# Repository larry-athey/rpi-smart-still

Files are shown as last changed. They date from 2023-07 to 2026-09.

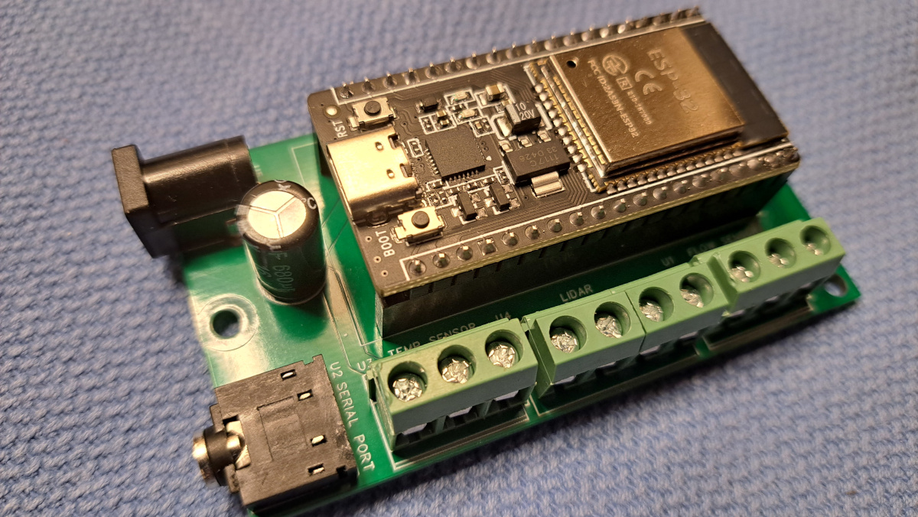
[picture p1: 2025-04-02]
Diagrams/LIDAR Hydrometer Reader/Bird-Brain-PCB-Assembled.jpg

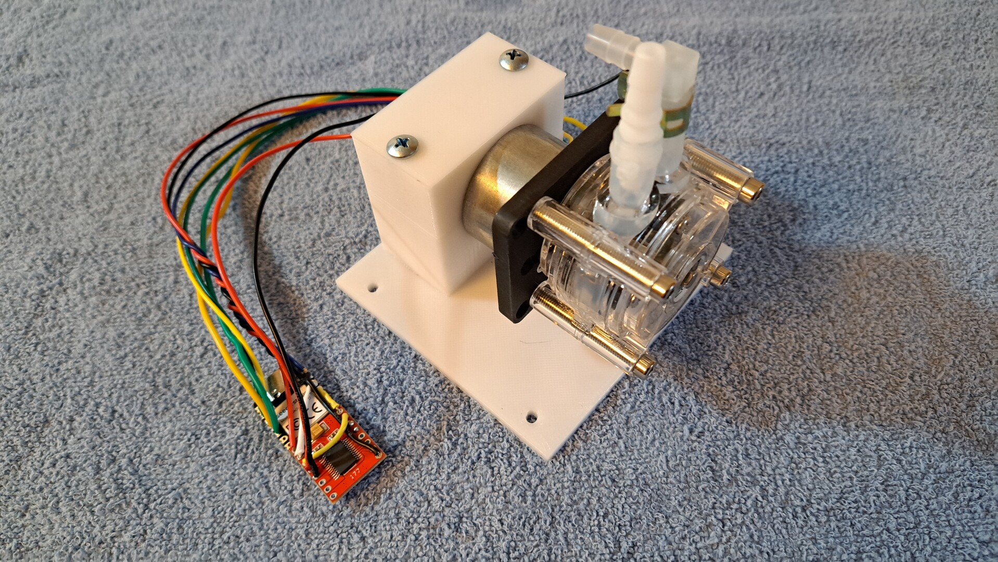
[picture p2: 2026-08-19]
Diagrams/Dephleg Driver/Dephleg Driver 1.jpg

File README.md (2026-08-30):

# RPi Smart Still
Raspberry Pi (or clone) and Arduino/ESP32 powered smart still controller system. Originally designed around the Still Spirits T500 column and boiler, but can be easily added to any other gas or electric still with a dephlegmator. Safe to say that this is the world's first add-on smart still controller because I looked for one before I was forced to build my own. My only other option was to spend $15K on a Genio or iStill...Uh, pass - I'll build one from scratch.

**Please refer to the [Wiki](https://github.com/larry-athey/rpi-smart-still/wiki) for more information and setup/usage instructions.**

**NEWSFLASH:** _Complete [turn-key systems](https://panhandleponics.com/rpi-smart-still-turn-key-systems/) are now available by special order. These systems can vary from the controller-only, all the way up to the controller + LIDAR Hydrometer Reader + Boilermaker + 10" Android tablet + dedicated WiFi router, all pre-configured and ready to plug in._

You may contact me directly at https://panhandleponics.com/contact<br>
Subscribe to the official YouTube channel at https://www.youtube.com/@PanhandlePonics

**Facebook Idiot:** _Why would you bother?_<br>
**Me:** It's only a "bother" for somebody who couldn't do it on their best day. I'd rather have nicer things.

_...No, I don't use AI to design and build my projects, I actually still know how to use my brain..._

---

_**NOTE:** Contrary to a popular misconception, this system does not take away your ability to manually run your still. This system is actually completely stupid until you manually run your still with it and make notes that you would then use to create programs. There is no AI in use here! Every still is different and requires a training period before this system can begin replaying distillation runs. Again, please refer to the [Wiki](https://github.com/larry-athey/rpi-smart-still/wiki), reading is fundamental!_

<br>

Let me start off by saying that I'm no master distiller and I don't pretend to be one. YouTube and other social media sites already have more than enough self-idolizing hacks and frauds _(usually sporting a Popcorn Sutton photo as their profile picture)_ who think that they're legends in the distilling world and should be on the cast of Moonshiners _(a'la, "Cyrus Mason" and "Windsong", the Still'n The Clear charlatans)_. **I'm just a nobody hobbyist, not an internet celebrity or a deluded podcaster wannabe, and I most certainly do not idolize reality TV "stars".**

The main focus of this project is to read temperatures and control the heating & cooling water via servos while monitoring the results based on whether it's a pot still or reflux run. Also, be able to control these actions if a person wants to maintain a minimum proof in a pot still run. Plus, be able to shut down a pot still run once a minimum proof has been reached. Lastly, shut down the still if the output flow rate drops below a chosen flow rate.

This project is also not intended to replace things like the **Airhead** or **MyVodkaMaker**, this is meant to be added to an existing higher volume still that can deliver more product per hour. If anything, it's intended to provide a person **most** of the conveniences of a Genio or iStill using your own existing equipment and save you from a $15,000 _(or more)_ investment. The main controller costs less than $500 to build and works with any web browser.

Even though the still that I originally used is the Still Spirits boiler and their copper T500 column, this system will work with any other personal still as long as it has a dephlegmator. I don't have the room for anything larger and don't need to upgrade because of how little I actually drink. I just do distilling as a hobby and for this project. Electronics, robotics, and programming are also hobbies of mine. So, here we are. LOL!!!

Contrary to what you see in YouTube videos and in that T500 users group on Facebook, it actually can be used for more than just making flavored distilled sugar wash. I'm not on Facebook anymore, but when I was, I just had to shake my head at all of those T500 users who thought they were actually making whiskey by dumping a bottle of essence in some 90% lighter fluid and then complaining about how bad it tastes. LOL!!!

The T500 column in its default configuration that Still Spirits designed it is a one-trick-pony. Reflux only, no pot still flavor, pretty much only good for making neutral spirits. Once a person controls the condenser and dephleg cooling separately, it's then possible to run a T500 in pot still mode and have a more controlled reflux system. This allows you to target a higher proof than the constantly declining proof in pot still mode, while still retaining pot still flavor. Best of all, this can be accomplished totally hands free.

This is a little bit of a juggling act to do manually, no matter what still you happen to use, but especially so with a T500. But it's not hard to automate this and stop your run once the still can no longer deliver the target proof. From that point, you can flip the still controller over to maximum reflux mode to finish stripping out all of the remaining ethanol as a totally neutral spirit, which can then be added to another run.

_**NOTE:** It's upon on the distiller themselves to take cuts because there is no way to make flavor determinations electronically without the use of gas chromatography. Please see my [Cutting Board](https://github.com/larry-athey/cutting-board) project for a more simplified alternative that automatically swaps out jars once they are full._

---



---



---



---



---



---



---



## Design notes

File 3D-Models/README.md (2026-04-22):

# 3D Model Notes

**Controller Case** - This folder contains all of the models for the 10x10x3 inch case for the full controller and valves.

**LIDAR Hydrometer Reader** - This folder contains all of the models associated with the LIDAR Hydrometer Reader project.

**Misc** - This folder contains miscellaneous models used for wire and hose routing.

**Prototype Projects** - This folder contains old models that were created along the way during the prototype process.

**Raspberry Pi Hat** - This folder contains models related to Raspberry Pi Hat installation.

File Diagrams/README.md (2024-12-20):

Raspberry, Orange, Banana, Banana Zero

As of October 1, 2024 I am now only encouraging and supporting builds based on the Raspberry Pi Hat. If you are the adventurous type, you are still more than welcome to build a prototype system. I'm only maintaining that information here and the original videos on the prototype system so people can gather a better understanding of how things work at a low level. As time allows, I will be creating new videos related to builds based on the Raspberry Pi Hat.

The official hydrometer interface for the system is the Bird Brain _(LIDAR hydrometer reader)_ and capacitive flow sensor. You are still free to use the older Load Cell Hydrometer if you wish, but it is no longer considered a supported project. You will need to enable support for the Load Cell Hydrometer by changing the settings.hydro_type database field value to 0 in order to use it with the system.

**NOTE:** _While the name "Raspberry Pi" is used frequently here, please keep in mind that this system is compatible with Raspberry Pi clones as well. It's no big secret, the Raspberry Pi drought caused a lot of clones to be created that actually out-spec and out-perform the original at drastically lower prices. As of the Model 5, the company has made it clear that they are no longer concerned with the functionality of older models and Raspbian 12 has broken a lot of their capabilities. As well as rendering **years** of online documentation no longer valid._

**ALSO:** _Due to this blatantly underhanded money grab to recover their losses from the drought, I'm now only supporting Raspbian up through version 11 on pre Model 5 Raspberry Pi units and focusing more on supporting Debian for ARM (Armbian) on Raspberry Pi clones._

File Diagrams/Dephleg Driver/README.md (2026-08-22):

# Dephleg Driver

This is an optional replacement for the motorized ball valve that manages the cooling water flow to the dephlegmator. The reason for this option is because many people don't run on public utility water pressure. When people use impeller driven pumps to run their cooling water, in every case I've seen, there isn't enough pressure to continue pushing water through the ball valves if they're choked down to 30% or less.

The problem with this is that there becomes no balance between too much reflux where you get no output from your still and simply switching right back to pot still mode. The Dephleg Driver solves this problem by replacing the ball valve with a PWM driven peristaltic pump. These naturally have a low flow rate simply due to the nature of their design but they have plenty of pressure to maintain the water flow over pretty much any distance you can throw at it.

No modifications to the RPi hat are needed beyond unplugging the logic level shifter chip closest to the L298N motor driver. The Dephleg Driver has only 7 wires, two connect to a pair of open pins on the logic level shifter socket, two to the original ball valve limit switch terminals, one to the +5 volt terminal, one to the +12 volt terminal, and one to a ground terminal. Connect the water lines and the upgrade is complete, all water flow problems solved.

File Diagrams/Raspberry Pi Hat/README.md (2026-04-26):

# Important Note

While each of these RPi Hat printed circuit boards has a footprint for a 5 volt 5 amp buck regulator, you will likely find that every one of them that size can only run a Raspberry Pi Model 3B+.

If you are going to use anything newer or a higher performance Banana Pi or Orange Pi, I am going to recommend that you use an external 12 volt to 5 volt regulator, such as those that you would use in an automotive setting. For example [this one](https://www.amazon.com/dp/B0FYNCSV2Z) as shown below.

The smaller ones that fit in the footprint on the printed circuit boards will go into overload shutdown and will stay latched in shutdown until all power has discharged. I realize these are bulkier, but the little ones just can't handle the current draw of today's single board computers.

---

RPi Hat<br>

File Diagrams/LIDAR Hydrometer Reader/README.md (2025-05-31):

Printed circuit board design by [James "The Doc"](https://www.youtube.com/@TheDocChannel) of Ireland. This is for either a wide or standard format 38 pin ESP32 board. C1 value isn't labeled on the board, 470uf at 15 volts would be a good value here.

**HELPFUL NOTES**
- The 1 meg resistor _(R1)_ actually works better when replaced by two of them in series _(2 megs)_
- The wires to the flow sensor capacitor plates should be shielded inside of a grounded steel braid
- Choose a low profile capacitor for C1 so it doesn't block the USB port on the ESP32
- An absolutely dry flow sensor will yield erratic and unreliable readings on the controller dashboard
- You should periodically flush the flow sensor with vinegar to clean the capacitor plates

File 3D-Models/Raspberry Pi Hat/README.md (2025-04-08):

# 3D Model Notes

As you can see by [the photo](https://github.com/larry-athey/rpi-smart-still/tree/main/Diagrams) of the four Raspberry Pi (and clones) in the Diagrams directory, the last one is a Model Zero style. If you are not using a Model Zero, you will need to clip off the center pair of mounting stand-offs from the **RPi + Hat Mounting Plate.stl** model.

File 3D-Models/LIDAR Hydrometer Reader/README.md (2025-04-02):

# 3D Model Notes

**34-Copper-flow-Sensor** - This folder contains models related to the [3/4" copper pipe flow sensor](https://www.youtube.com/watch?v=uXPyjsHgtic) designed by [James "The Doc"](https://www.youtube.com/@TheDocChannel) of Ireland. This includes the mounting arm that attaches to the center column of your parrot.

**BB-Case-Bottom.stl** - This is the bottom (or base) of the Bird Brain PCB case. This is a slip together case so the top can be quickly removed in order to see the blue LED which indicates memory slot updates while you are calibrating the hydrometer. It's up to you what type of filament you print this case with, PLA is fine here.

**BB-Case-Cover.stl** - This is the top half of the Bird Brain PCB case. It is recommended that you attach the case bottom to the base of your proofing parrot and leave enough space for this cover to slip on and off.

**Flow-Sensor-Bottom.stl** - This is the bottom part of the 3D printable flow sensor vessel that inserts into the 1-3/8" (35mm) receiver cup of your proofing parrot. This must be printed with PETG using 0.1mm layers due to the size of the weep holes in the stand pipe. Or, if you have an SLA resin printer, that would be better yet. Check your resin's technical data to verify that it can stand up to ethanol.

_**NOTE:** If you use an FDM printer, the bottom part of the flow sensor **must** be printed with PETG filament, not PLA! This is the same plastic that you will find bargain basement bottles of booze bottled in. PLA will progressively deteriorate if exposed to ethanol. While PLA is made mostly from corn, other chemicals used in its manufacture really aren't safe for distillation or food/drink storage._

**Flow-Sensor-Cap.stl** - This is the cap for the above mentioned flow sensor vessel. It is suggested that you print this using TPU so that it can expand while inserting the copper capacitor plates and the DS18B20 temperature sensor. There is a 10mm hole to accept a small funnel to function as your condenser receiver or 1/4" ID silicone tubing from the output of a Still Spirits T500 column.

**Flow-Sensor-Plate-Spacer.stl** - This goes on the end of the copper capacitor plates inside the flow sensor vessel to prevent them from touching each other. This should also be printed with TPU so it's easier to insert the capacitor plates. The plates should reach all the way to the bottom of the vessel, cut two copper strips 55mm x 10mm and bend a 5mm tab at the top to solder the wires to.

**Hydrometer Reflector.stl** - This is the circular reflector that goes at the top of your hydrometer. You should print this in PLA using 0.1mm layers, this will only be two layers tall. While you could print this with a single 0.2mm layer, it will likely tear when you put it on your hydrometer. Depending on your hydrometer, you may need to slightly notch the center hole to make it fit.

**LIDAR Sensor Mount - Back.stl** and **LIDAR Sensor Mount - Front.stl** - These are the two halves of the LIDAR sensor mount that attaches to the overflow cup of your parrot. You will need two 10mm M2 self tapping screws to hold the two halves together and clamp it in place on your parrot. This can be printed with any type filament.

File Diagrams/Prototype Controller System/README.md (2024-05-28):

I'm really not good at diagrams because I can't seem to get a decent grip on those kinds of tools. Mainly because their component libraries always seem to never include all of the same components that I'm using. I'm still hunting around for something that will work for me and not require me to change any designs.

New additions here by [FireflySE](https://github.com/FireflySE) include **Still-Controller-and-Monitor-Schematic.png**, **Still-Monitor-and-Controller.fzz** _(Fritzing project file for building the prototype system)_ and the **Raspberry Pi Hat** directory _(to simplify assembly if the prototype system is too daunting)_. Be sure to see page 8 of the [Wiki](https://github.com/larry-athey/rpi-smart-still/wiki) regarding his addition of auxiliary relays to the Raspberry Pi Hat for running pumps.

Prepped and tested RPi Smart Still Hats, LIDAR Hydrometer Readers, and 3D printed parts from the /3D-Models/ directory may be ordered from https://panhandleponics.com/rpi-smart-still-controller-components/ if you'd like to save yourself some time or if you simply aren't comfortable with soldering and 3D printing.

**NOTE:** _Keep in mind that Fritzing doesn't include all of the same components that I use, so there have been some substitutions used. Be sure to keep this in mind and don't try to use things like a DHT22 in the place of a DS18B20, the code doesn't support a DHT22._

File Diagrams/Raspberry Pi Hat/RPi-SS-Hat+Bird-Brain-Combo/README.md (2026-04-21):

This is a 4-layer version of the RPi Hat by [FireflySE](https://github.com/FireflySE) of Sweden, with the LIDAR Hydrometer Reader built-in and without the stepper motor driver _(Boilermaker only)_.

I personally have not tried this board yet, but you will most definitely need to use shielded cables for **everything** related to the hydrometer, especially the flow sensor. Keep in mind that the flow sensor is a capactitor and the longer the wires to it, the larger the capacitor becomes.

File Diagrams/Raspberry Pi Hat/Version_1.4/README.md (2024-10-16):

This is a 4-layer version of the RPi Hat by [FireflySE](https://github.com/FireflySE) of Sweden, and is capable of running everything up to a Model 5 and its clones. Depending on your location and where you get printed circuit boards made, the 2-layer version 1.3 boards could save you money over the price of the 4-layer version 1.4 boards. JLCPCB adds a nearly $40 surcharge if you are in the USA, so even with PCBway's higher prices, the 2-layer version 1.3 boards from them will be the least expensive option.

The issue with the logic level shifters in the v1.1 and v1.2 boards is fixed in this version.

As stated in the [Wiki](https://github.com/larry-athey/rpi-smart-still/wiki), this system will run perfectly fine on a Model 3 B+, even with a built-in screen and full desktop environment. A Model 4 will make a full desktop based system will provide a more responsive user interface, but a Model 5 is complete overkill and kind of a waste of such a high powered computer.

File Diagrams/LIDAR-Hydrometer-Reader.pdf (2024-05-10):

I almost always base my projects on PCB clones of breadboards to make planning easier. In rare cases, I will use plain old point-to-point boards if it doesn’t involve a lot of jumper connections. Here’s a link to the boards I used in the photos.

https://www.amazon.com/gp/product/B0BP28GYTV/

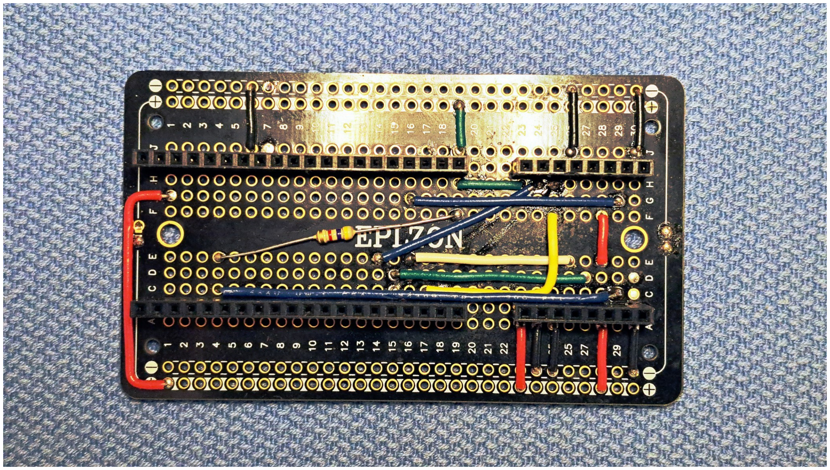
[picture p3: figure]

This project has quite a handful of soldered jumper wires. But, at least wires aren’t as critical as things like electrolytic capacitors and diodes that have a polarity that has to be honored or you’ll let out all of the magic smoke. As you can see, there is only a 4.7K pull-up resistor from the +3.3 volt pin of the ESP32 to the GPIO 15 pin.

Both negative buses on the PCB are connected together, but the top positive bus is +3.3 volts and the bottom one is +5 volts. The +3.3 volt bus is supplied by the ESP32’s onboard 600ma voltage regulator. This is more than enough current for the VL53L0X, everything else connected to this device runs on +5 volts.

As with the Load Cell Hydrometer, the far left pins on the ESP32 socket are clipped off because the socket strips are 20 pin and the ESP32 has 19 pins on each side. The socket strips to the right of the ESP32 are the bus for connecting the 5 volts and serial communications from the RPi Smart Still Controller, the DS18B20, flow sensor, and VL53L0X.

Below is how I have connected things to this bus. The bottom row is “A” and the top row is “B”. I number the pins 1 to 8 from left to right.

Please note that the serial communications jack uses the tip for the TX line and the ring for the RX line.

Power supply +5 volts 1A | 1B VL53L0X +3.3 volts
Power supply negative 2A | 2B VL53L0X SDA
Serial comm jack gnd 3A | 3B VL53L0X SCL
Serial comm jack TX | 4A | 4B VL53L0X negative
Serial comm jack RX | 5A | 5B
DS18B20 +5 volts | 6A | 6A Flow sensor +5 volts
DS18B20 data | 7A | 7B Flow sensor pulse
DS18B20 negative | 8A | 8B Flow sensor negative

If you follow the wires in the above photo and the pin definition constants in the source code, you shouldn’t have any problem wiring things correctly. Below is an image of the pin layout for the 38 pin ESP32 board that I use. This is pretty much standard for all 38 pin boards.

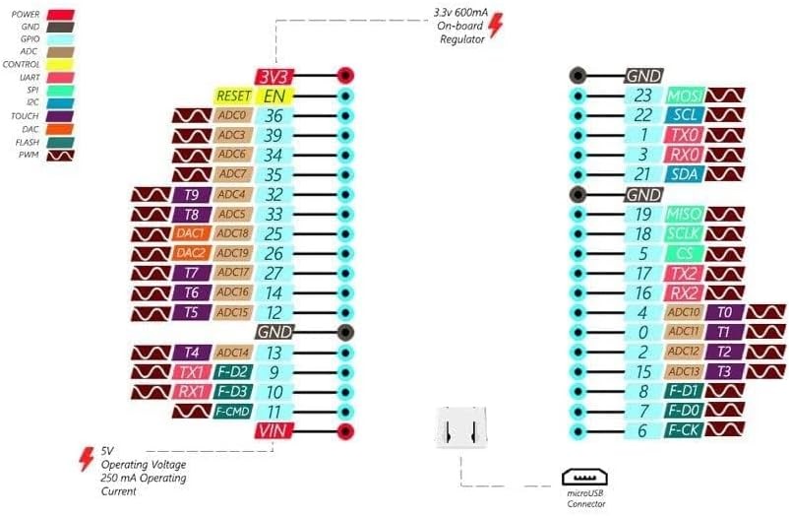
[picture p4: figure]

Yes, I realize that 38 pins is entirely overkill for what I’m doing in this project, but I only buy 38 pin boards because they’re cheap and always leave me room to grow. Smaller boards really don’t save me a whole lot, usually less than a dollar.

In case you are unfamiliar with this VL53L0X device, this is a LIDAR sensor, which is a what “laser tape measures” use. If you have ever used one, you probably saw the procedure in the owner’s manual that shows you how to measure the height of a telescopic pole. A reflector is placed atop of the pole and you measure from the ground-up. This is how the hydrometer reader works, a paper disk is placed at the top of the hydrometer and its height is measured to obtain the ABV reading.

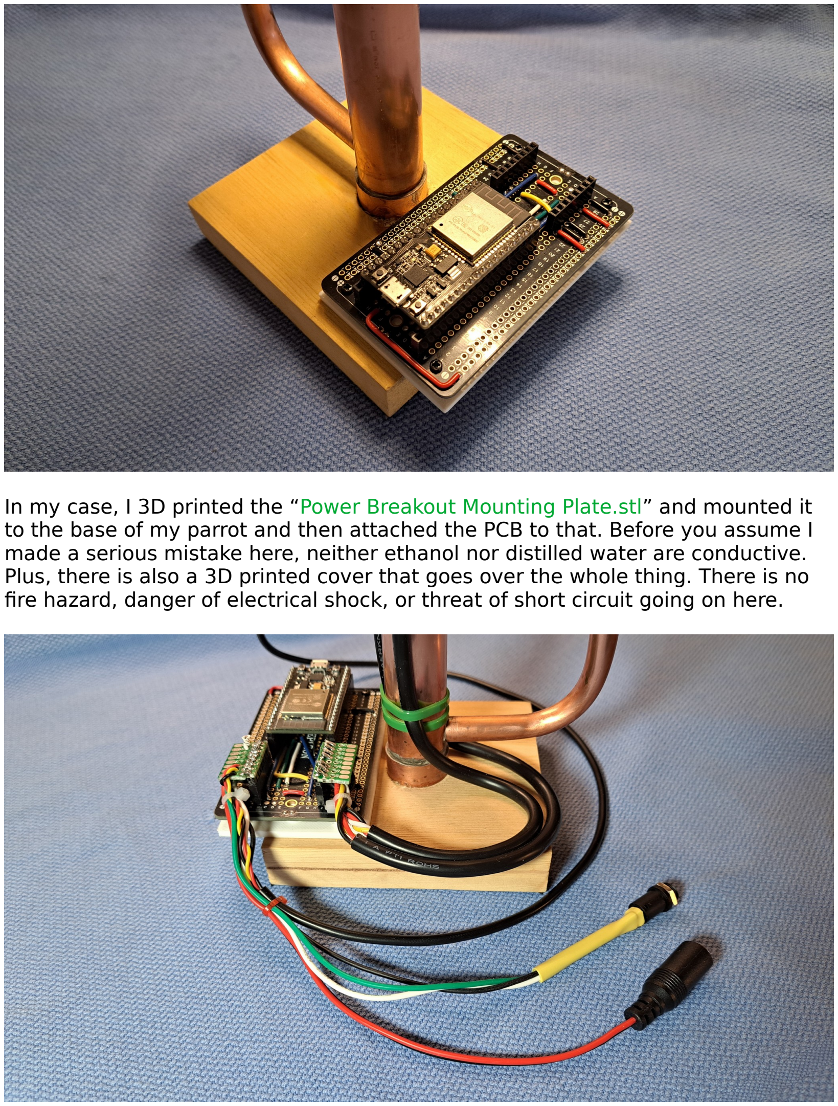
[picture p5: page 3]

In my case, I 3D printed the “Power Breakout Mounting Plate.stl” and mounted it to the base of my parrot and then attached the PCB to that. Before you assume I made a serious mistake here, neither ethanol nor distilled water are conductive. Plus, there is also a 3D printed cover that goes over the whole thing. There is no fire hazard, danger of electrical shock, or threat of short circuit going on here.

All of the wires are soldered to 8x3 pin sections of point to point PCB material with an 8 pin header to plug into the socket strips. The DS18B20, power, and the serial communications wires are intentionally ganged together on one plug so the whole thing can be easily unplugged from the RPi Smart Still Controller and carried away so you can dump the parrot.

The wires on the right are for the VL53L0X and flow sensor and are zip tied to the parrot center tube. Yes, I realize that I could have used smaller cables for this, but I used what I had since this is only a prototype design. If I was out to win a beauty contest here, I’d contact Wayne Herbert at Ozark Still Works (https://ozarkstillworks.com/) to build me a custom parrot with a separate tube going up one side to run the wires up through.

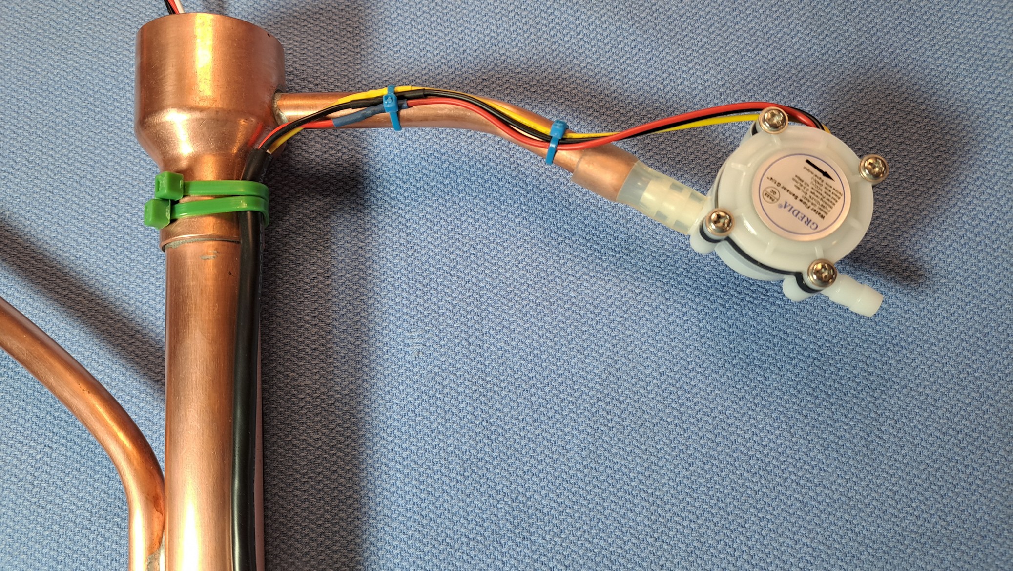
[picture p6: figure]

A hall effect flow sensor (https://www.amazon.com/gp/product/B07RF57QF8/) has been attached to the output tube of the parrot using a piece of ¼” silicone tubing as the coupler. Depending on the one you get and the amount of flow coming out of your parrot, you may need to rotate it to a different angle to get it to track your ethanol flow correctly. Mine is rotated upright for this picture to show the label.

The way this unit works is that every second, the ESP32 checks to see how many pulses there have been since the last check [0 to 255]. These readings are stored in an array of 100 readings and they are averaged every time a serial data block is sent to the RPi Smart Still Controller as a floating point value.

If you don’t intend to use RPi Smart Still Controller programs that shut down a run when the flow drops below a certain value, you can safely leave this device out of the mix. The ESP32 won’t hang if this device doesn’t exist.

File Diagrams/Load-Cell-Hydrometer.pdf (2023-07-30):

I almost always base my projects on PCB clones of breadboards to make planning easier. In rare cases, I will use plain old point-to-point boards if it doesn’t involve a lot of jumper connections. Here’s a link to the boards I used in the photos.

https://www.amazon.com/gp/product/B0BP28GYTV/

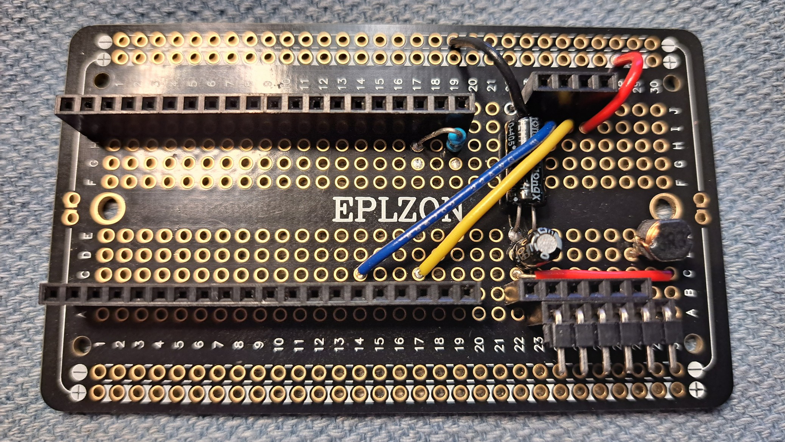
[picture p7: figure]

As you can see, there are a few external components used. From PCB pins 17H to 19H there is a 4.7K pull up resistor which is from the 3.3V pin of the ESP32 to GPIO 36 for the DS18B20 OneWire temperature sensor.

To the right of the ESP32 socket, there Is a socket for an HX711 load cell amplifier board. Below its 6-pin row, there is another 6-pin socket offset by one pin to the right. This is where the load cell connects, but it is offset so that a noise filter can be inserted into the path of the red wire (E+) of the load cell.

The pins on the load cell socket are black (E-), white (A-), green (A+), skip two pins, and red (E+) at the far right end.

The noise filter is Sparkfun’s design, not mine. The red (E+) wire first runs through a 3.3 uH inductor before connecting to the E+ pin on the HX711. Two capacitors in parallel are placed across the E+ and E- pins of the HX711. This is because there is no such thing as an 10.1 uF capacitor, so you need to use a 10 and a 0.1 in parallel. I have no idea how they arrived at that value, but I’ll just go along with it and do what they did.

The top row of pins are connected to the 5 volt supply and the I2C GPIO pins of the ESP32. Yellow to clock (GPIO 22) and blue to data (GPIO 21).

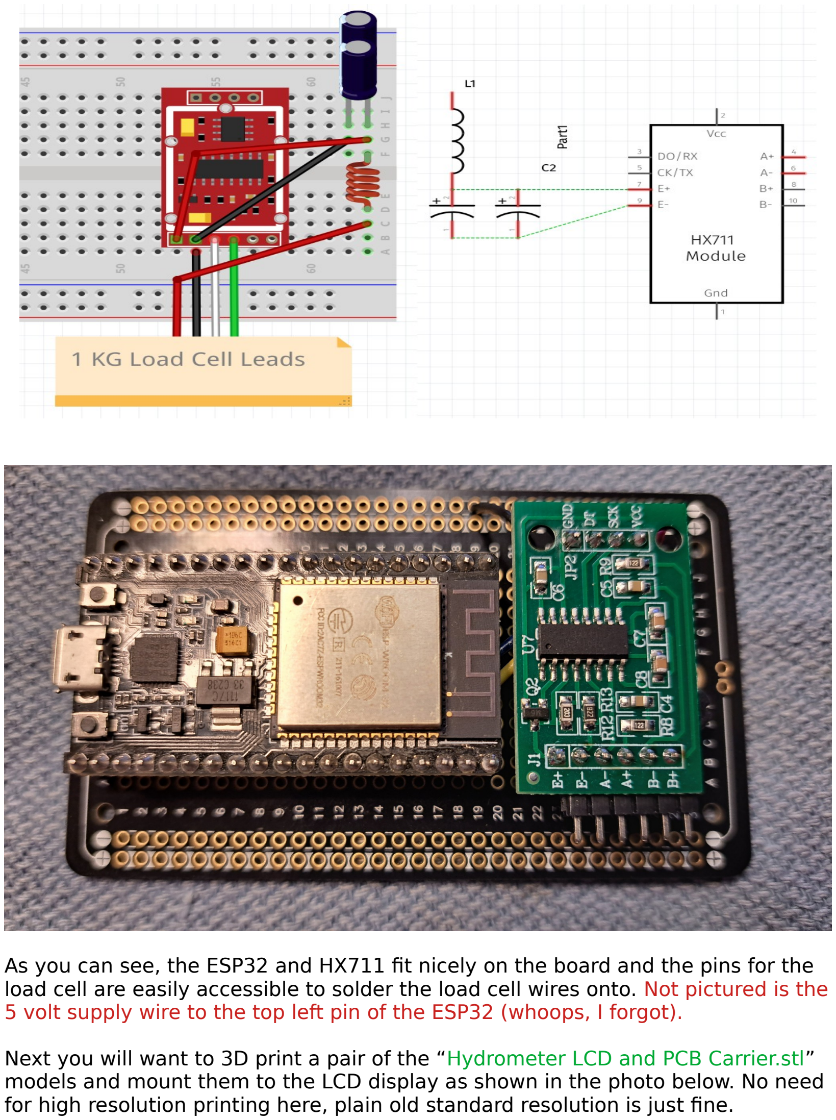
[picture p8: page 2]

As you can see, the ESP32 and HX711 fit nicely on the board and the pins for the load cell are easily accessible to solder the load cell wires onto. Not pictured is the 5 volt supply wire to the top left pin of the ESP32 (whoops, I forgot).

Next you will want to 3D print a pair of the “Hydrometer LCD and PCB Carrier.stl” models and mount them to the LCD display as shown in the photo below. No need for high resolution printing here, plain old standard resolution is just fine.

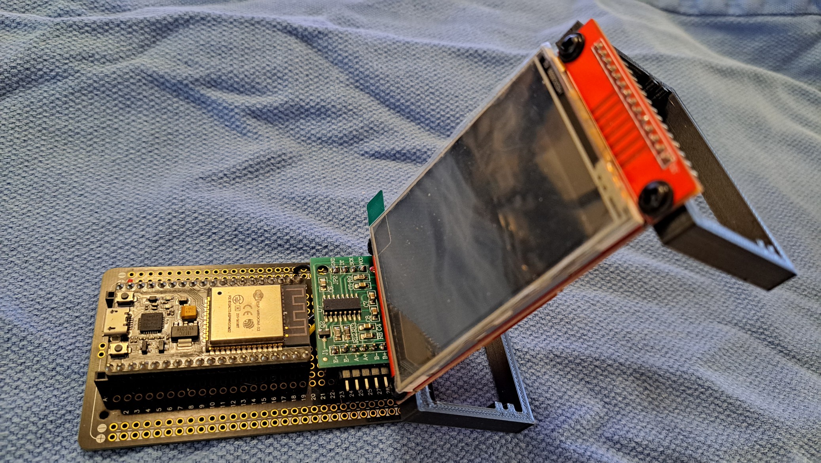
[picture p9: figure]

The display that I’m using here is the ever so common ILI9341 320x240 color LCD/TFT display that uses SPI communications. Here’s an Amazon link for it.

https://www.amazon.com/gp/product/B09XHJ9KRX/

The touch screen and SD card slot aren’t used here, so we only need to connect the first 9 pins on the unit. I simply solder wires onto the pins rather than using push-on connectors. If you want to install push-on connectors, have at it. I’m 50% blind and can’t get it right, so I gave up.

This is another reason why I use those PCB clones of a breadboard, the numbers on the rows and columns of pin holes really helps when connecting things to the GPIO pins of an ESP32. For example, I know the display’s CS line connects to GPIO pin 5 of the ESP32. I know that pin is 10th from the left in the above picture and that pin has a 10 right next to it on the PCB.

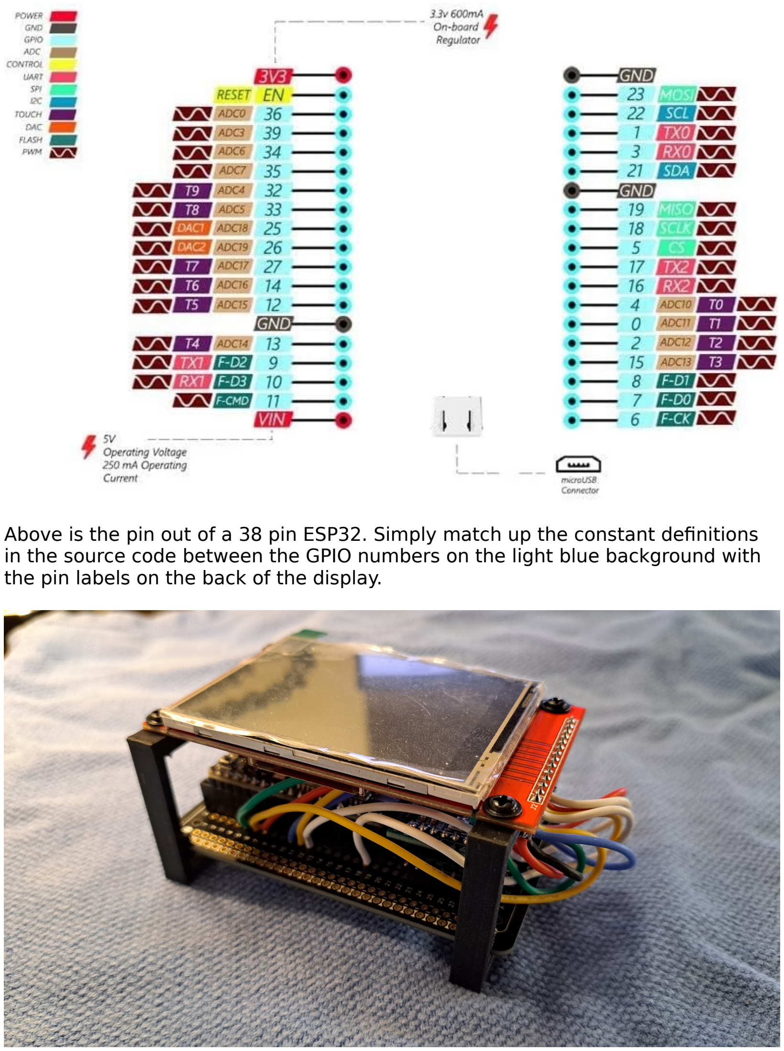
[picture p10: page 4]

Above is the pin out of a 38 pin ESP32. Simply match up the constant definitions in the source code between the GPIO numbers on the light blue background with the pin labels on the back of the display.

The extra slack in the wires to the display will leave everything still serviceable after it is installed in the enclosure. If you ever need to reprogram the ESP32 or replace the HX711 load cell amplifier, just remove the screws from the display and pull them out of their sockets.

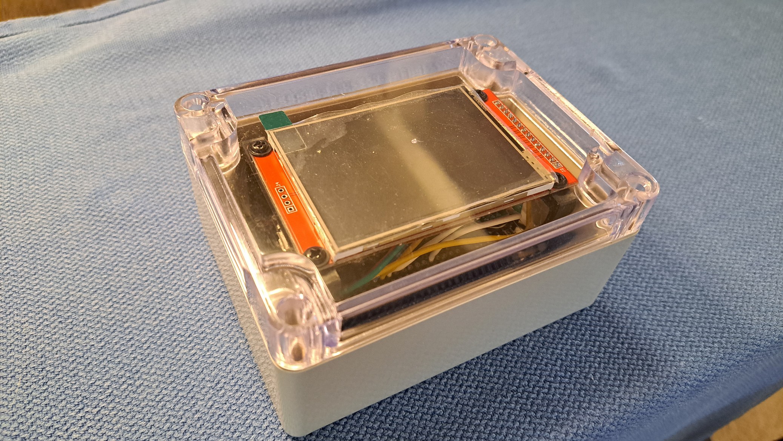
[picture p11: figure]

The enclosure is slightly over-sized, but this is necessary. Unfortunately, there is a mark in the middle of the top cover from the injection molding fill point. I have no idea if it’s possible to polish it out, but I’m not going to bother trying. It’s not that big of a deal. Below is an Amazon link to the enclosure.

https://www.amazon.com/dp/B07BPPKF2C/

We need to drill five holes in the back for the power and serial connector jacks and three smaller holes for the load cell, temperature sensor, and flow sensor leads. We will wait to do the soldering of these leads to the PCB after they are installed on the frame that holds everything together.

Before we go any further, you should 3D print the models “Flow Sensor Housing.stl” and “Condenser Feed Retainer.stl” at the highest resolution that your printer can do. These parts need to be precise, strong, and as waterproof as you can get them. I’ve broken off screw heads mounting high resolution 3D printed parts with 30% infill, breaking them off with pliers is by no means a simple task.

I don’t expect everybody to use my design, mine is dual purpose so that it can be hung on the wall with picture hangers or around a 2” pipe such as a still column. So mine is made with two 14” pieces of a red oak 1x4 plank with the two models “Hydrometer Frame – Left.stl” and “Hydrometer Frame – Right.stl” on each end.

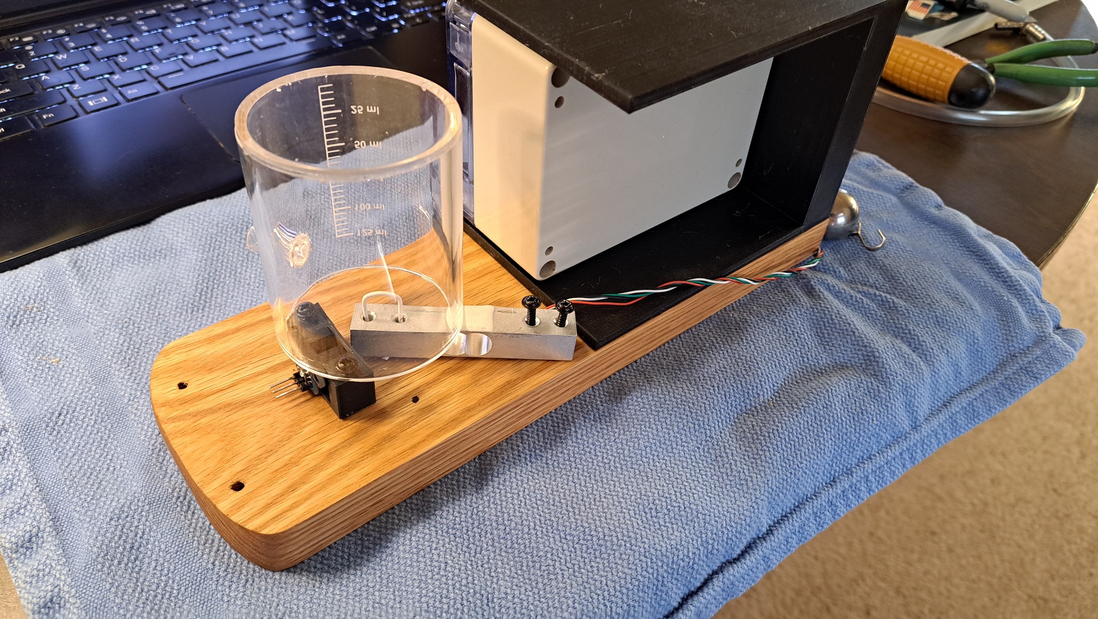
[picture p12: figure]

In the above photo, you can see a general idea of how the load cell and flow sensor are situated. The dot on the board between the two is where the hole for the DS18B20 temperature sensor cable is drilled to feed through.

As for the hydrometer frame end pieces, it’s up to you what resolution that you want to print them at, if you use this design plan. I just used plain old standard resolution because they’re only structural pieces and don’t need to be waterproof. The right side of the frame still took 14 hours to print at that resolution.

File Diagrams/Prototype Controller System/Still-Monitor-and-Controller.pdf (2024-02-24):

I almost always base my projects on PCB clones of breadboards to make planning easier. In rare cases, I will use plain old point-to-point boards if it doesn’t involve a lot of jumper connections. Here’s a link to the boards I used in the photos.

https://www.amazon.com/gp/product/B0BP28GYTV/

There are four PCBs that require soldering and that’s the power break out board (pictured below), the valve control board, the heating stepper control board, and the interface board. Luckily, none of them involve anything real complicated.

## Power Break Out Board

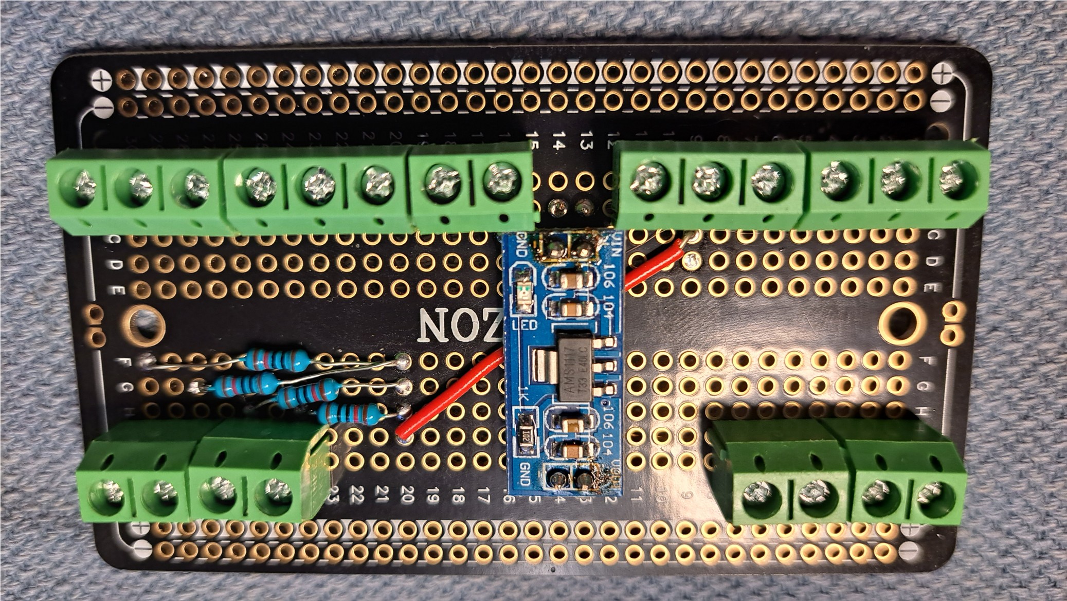
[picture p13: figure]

The power break out board receives 5 volts from the buck regulator and provides a set of power distribution terminals. Six for 5 volts, four for 3.3 volts, eight grounds, and set of four pull up resistors for the GPIO pins that monitor the servo valve limit switches.

The pull up resistors are 10K and feed from the 5 volt supply. The 3.3 volt supply was an after thought, or I would have fed 4.7K resistors from there.

The little blue board in the middle is an AMS1117 3.3 volt 800 mA regulator that feeds from the 5 volt supply and outputs to the four terminals in the upper left. Below is a link to these regulators.

https://www.amazon.com/gp/product/B074FDLCLB/

Thus far, I am only using the 3.3 volt supply to power the heating stepper motor control board and a small speaker that I use for the Raspberry PI audio output.

## Valve Control Board

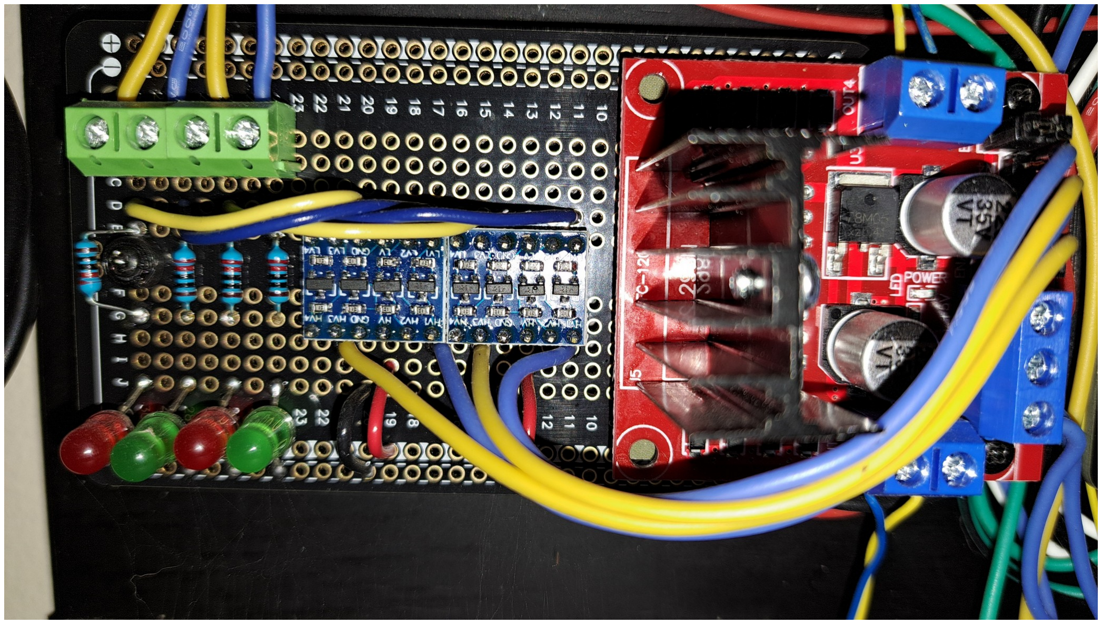
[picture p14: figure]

The condenser and dephlegmator valves don’t use stepper motors, but they have upper and lower limit switches. These use plain old DC motors and their position is merely tracked by how many milliseconds that they get power in either direction. This is the reason for the “Calibrate Valves” function of the smart still controller.

The motors are controlled by an L298N “H-Bridge” driver which is commonly used in robotics and RC cars. These drivers use 5 volt logic, so I2C logic level shifters are used in order for the 3.3 volt logic from the Raspberry PI GPIO pins to control them. This could also be done with a diode/resistor pair per pin, but I like simple.

If you look at the source code in valve.c you will see the GPIO pin assignments for the valve motors. Looking at the diagram below, the green header connects to the GPIO pins 25, 24, 21, and 20 from left to right.

The 4 pull-up resistors on the power break out board in the above connect to GPIO pins 23, 22, 19, and 18 which are for the limit switches in the valves. When these pins are pulled low by the limit switches, it tells the code in valve.c that the valve is at its full-open or full-closed position. See my YouTube video on this for details.

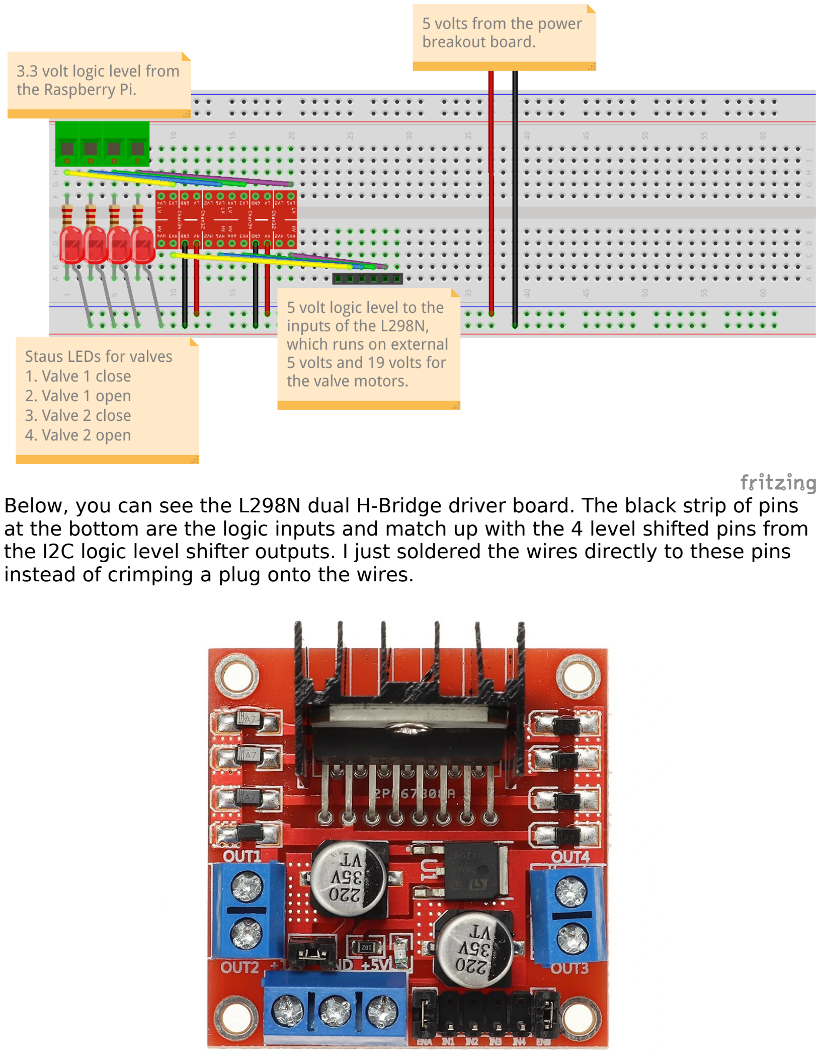
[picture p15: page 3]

Below, you can see the L298N dual H-Bridge driver board. The black strip of pins at the bottom are the logic inputs and match up with the 4 level shifted pins from the I2C logic level shifter outputs. I just soldered the wires directly to these pins instead of crimping a plug onto the wires.

As you look to the left of the logic pins, you will see the power connections for the driver board. Directly above those terminals is a jumper that you will want to remove. With the jumper in place, the driver can only be run by 12 volts since the onboard linear 5 volt regulator (LM7805) can’t handle any more than that.

The valve motors run on 9 to 24 volts and I use a 19 volt laptop charger brick to run everything. So I connect +19 volts to the left terminal, ground in the middle, and +5 volts to the last one. This allows the valves run at a higher rate of speed which is way more reliable than making them struggle along on 12 volts.

The operation of this driver is rather simple. If all the logic pins are low, nothing is output. If pin 1 is high, the outputs on the left put out 19 volts in one polarity, if 2 is high, then the polarity is reversed. Logic pins 3 and 4 do the same thing with the outputs on the right hand side. Only one logic input can be high at any time.

If the manufacturer changes the color coding of the wires, you will just need to do test runs to make sure that your valves are moving the correct direction. The wire colors are not standardized, different brands will likely use totally different colors. The yellow and blue wires on the outputs in the photo may not match yours at all.

## Parts Needed

4 LEDs and 220 ohm resistors (if you want activity indicators)

(Your choice of source, these aren’t specialized parts)

Screw terminal strips for PCBs

https://www.amazon.com/gp/product/B088LSS14J/

I2C logic level shifters

https://www.amazon.com/gp/product/B07F7W91LC/

L298N dual H-Bridge module

https://www.amazon.com/gp/product/B014KMHSW6/

Motorized stainless steel ball valve with limit switches (x2)

https://www.amazon.com/gp/product/B06Y16BDFG/

## Heating Stepper Control Board

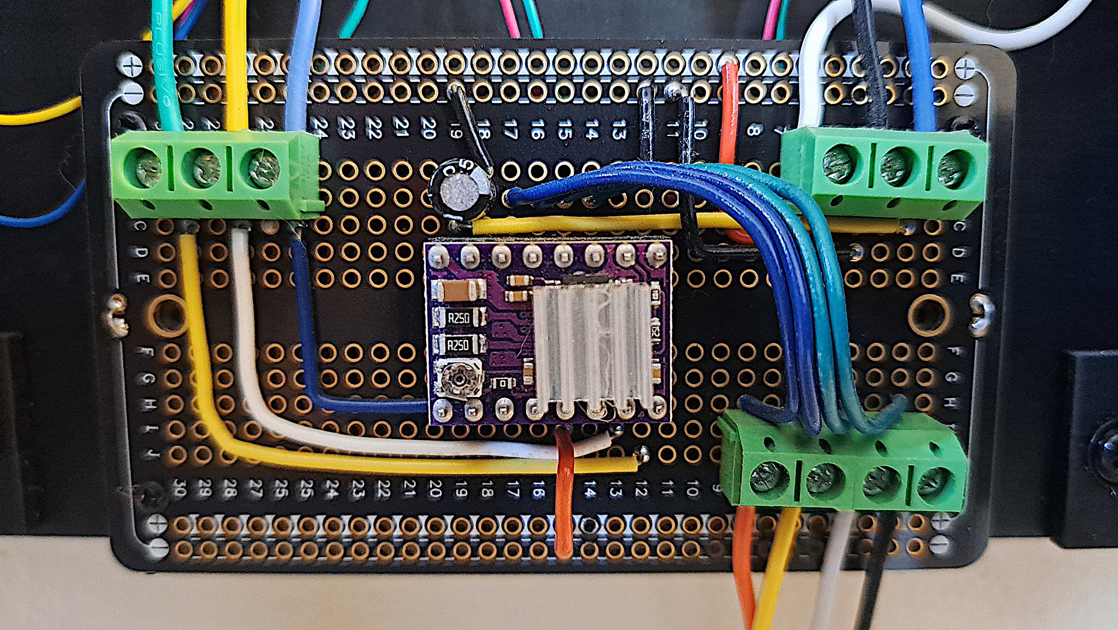
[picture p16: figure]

The first thing I would suggest that you do is watch the following tutorial video on the Raspberry PI and stepper motors, it will take all of the mystery out of this one. This smart still controller expects you to have a heating system that is controlled by rotary adjustment, whether it’s an SCR controller or gas fired burner and valve.

https://www.youtube.com/watch?v=LUbhPKBL_IU – Seriously, watch this video!

As you can see, there’s a whole lot of nothing to this board because it’s just point to point wiring from screw terminals to the stepper motor driver module and just a 100 uF electrolytic capacitor to smooth out any voltage drops. This is identical to what is used in the tutorial video.

The DRV-8825 is socketed rather than being soldered to the PCB. This is just one of those habits of mine because swapping out modules is the easiest way for me to troubleshoot them. I honestly can’t say if these are prone to burning out, but I would rather be able to just swap them out without any tools if one burns out.

Since there isn’t much point in a diagram here, due to the fact that’s it’s all just point to point wiring to the DRV-8825 module, I’ll just explain what each screw terminal is connecting to. It wouldn’t take a whole lot of effort to build everything in a much more attractive fashion than I did with breadboard PCB clones.

## Upper left terminal strip (left to right)

1. Raspberry PI GPIO 11, stepper direction control, module “dir” pin.
2. Raspberry PI GPIO 12, stepper pulse line, module “step” pin.
3. Raspberry PI GPIO 13, stepper enable/disable, module “sleep” pin.

## Upper right terminal strip (left to right)

1. +3.3 volt supply, module “reset” pin.
2. Ground to both module “gnd” pins.
3. +19 volt supply, module “vmot” pin.

NOTE: A 100 uF, 50 volt electrolytic capacitor is connected between the “vmot” pin and ground. This is a polarized capacitor, don’t connect it backwards!

## Lower right terminal strip (left to right)

1. Stepper motor coil 1a, module “a1” pin.
2. Stepper motor coil 1b, module “a2” pin.
3. Stepper motor coil 2a, module “b1” pin.
4. Stepper motor coil 2b, module “b2” pin.

The stepper motor coils aren’t critical as far as polarity, but connecting the coils to the wrong output pins of the module will make it run in reverse. If your motor runs the wrong direction when you increase your heating, just switch the coils or change the “Polarity” setting in the smart still controller, your choice.

DRV-8825 module

https://www.amazon.com/gp/product/B07XF2LYC8/

Nema 17 stepper motor

https://www.amazon.com/gp/product/B088BLQYDX/

Stepper motor mounting bracket

https://www.amazon.com/gp/product/B07JW6X9X2/

Flexible couplers (to connect motor to a potentiometer)

https://www.amazon.com/gp/product/B07JL1QYLS/

If you are going to be controlling a gas valve rather than a potentiometer, you will likely need to use something stronger than a Nema 17 stepper motor. But, I can’t see any problem with the DRV-8825 driving a stronger motor, you will just need to adjust it to match the current requirements of the stronger motor.

## Interface Board

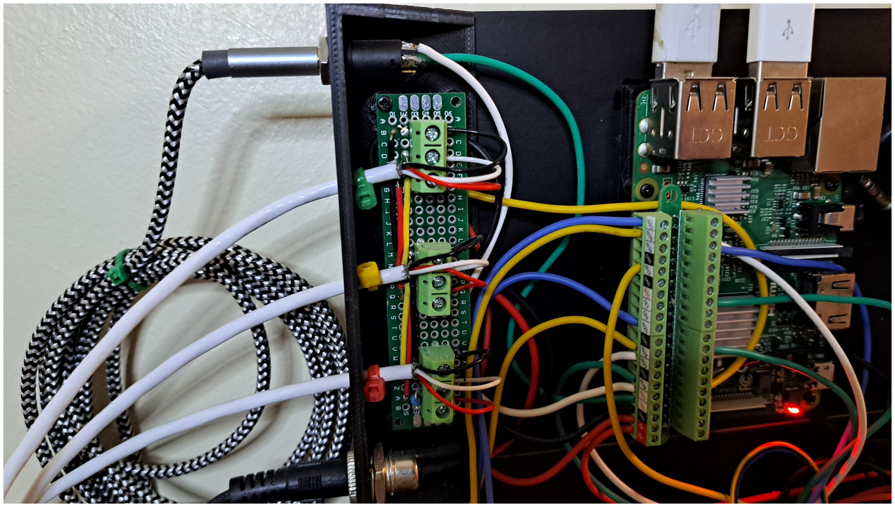
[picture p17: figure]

Not really a whole lot of anything special going on here, just a point-to-point board with three terminal strips to make it easy to replace the DS18B20 temperature sensors and provide +5 volts for the digital hydrometer. All three of the terminal strips are wired in parallel using +5 volts, data, ground from bottom to top with a 4.7K pull-up resistor across the +5 volts and data line.

The +5 volts is fed from the power break out board rather than from the GPIO bus because I don’t want to deal with any limitations imposed by the Raspberry PI circuitry. The temperature sensors and the hydrometer both require SOLID power.

Above the interface board is a stereo 3.5mm jack for the digital hydrometer serial data communications, below the interface board is its power supply jack. As I said, there’s really nothing special going on here, below are the GPIO connections.

1. DS18B20 data lines (all of them) to GPIO pin 4.
2. 3.5mm tip connection to GPIO pin 15 (PI serial RX).
3. 3.5mm ring connection to GPIO pin 14 (PI serial TX).

## Power Supply

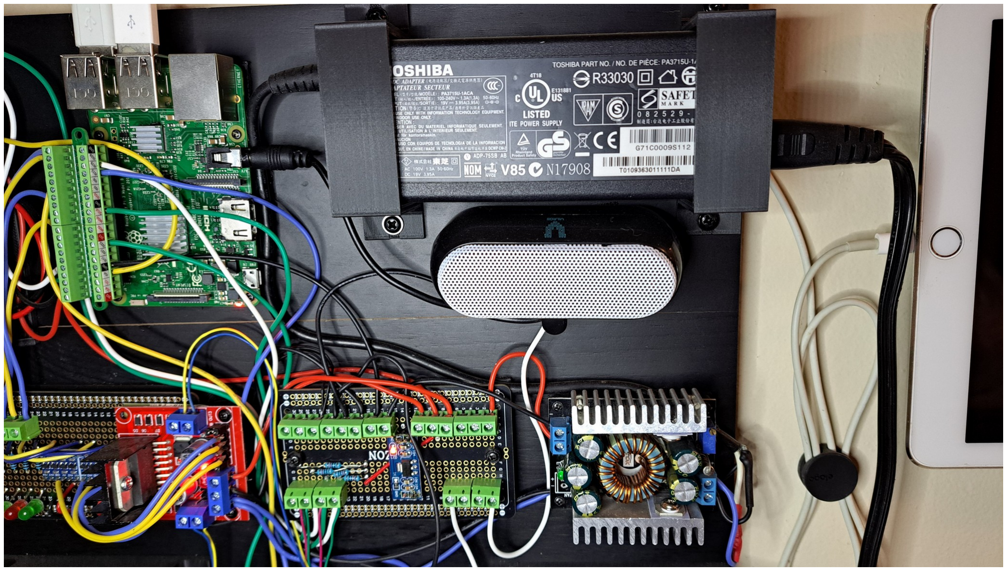
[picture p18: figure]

How you choose to power things is completely up to you, I certainly haven’t come up with the ultimate power supply here. I’m just using a discarded Toshiba laptop charger along with an adjustable buck regulator to give me a solid +5 volts. The laptop charger puts out +19 volts at about 4 amps which is plenty for this project.

Here’s the link to the buck regulator shown in the lower right.

https://www.amazon.com/gp/product/B00C4QVTNU/

The regulator is adjustable, you just connect it to the brick and put a volt meter on the output and adjust it down to about +5.2 volts with no load. Once you get the rest of the circuitry on there it will level out to an even 5.

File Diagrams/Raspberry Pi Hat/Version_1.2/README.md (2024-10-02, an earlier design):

If you refer to the picture of the assembled 1.2 board here, you can see that the logic level shifters have been omitted and bypassed. The reason being, the output of the first shifter in U16 wasn't connected, and channel 1 of the L298N was connected to the wrong pin. The version 1.1 boards also have this same problem. This is an easy fix, not a show stopper by any means.

**Most** L298N driver boards will work with 3.3 volt logic and won't require the logic level shifters, you will just need to test your boards. My original driver boards had 5 volt zener diodes on the inputs and required 5 volt logic, my new ones don't have these diodes on the inputs. The logic level shifters only exist here in case your L298N driver boards only work with 5 volt logic.

Also note, you need to make sure that the grounds between the terminals U2 and U6 are connected to each other, or your Raspberry Pi won't have a ground and won't power up. You can easily just solder a jumper wire between the two terminals if you want to.

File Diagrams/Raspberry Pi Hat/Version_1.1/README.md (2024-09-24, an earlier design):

For those who ordered version 1.1 of these printed circuit boards, there was a flaw in the design that needs to be fixed by cutting some foil traces and installing 5 jumper wires.

1. Cut the +5 volt supply line connecting to both ends of the J1 terminal bus (valve limit switch terminals).
2. Cut the foil to separate all 4 terminals in J1.
3. Solder in a jumper wire to reconnect the two open ends of the +5 volt supply line.
4. Solder jumper wires from each terminal to the end of R1/R2/R3/R7 that connect to the GPIO bus pins 18/19/22/23.

Refer to the photo Hacked_RPI-Smart-Still-V1.1_2024-08-17.jpg in this folder for a visual reference. I intentionally used wires of excess length to make the paths easier to follow.

You will also notice by the photo of the top of the assembled hat, I use a 5 volt buck regulator instead of the LM7805 and the filter inductor to reduce heat and bulk. This is now the standard design in the version 1.2 boards.

In version 1.2 of these boards, the red LEDs on the relays have gone away. You should install green LEDs in the place of the red relay LEDs and leave the original green LED mounting pads open. This will make version 1.1 boards functionally identical to the version 1.2 boards.

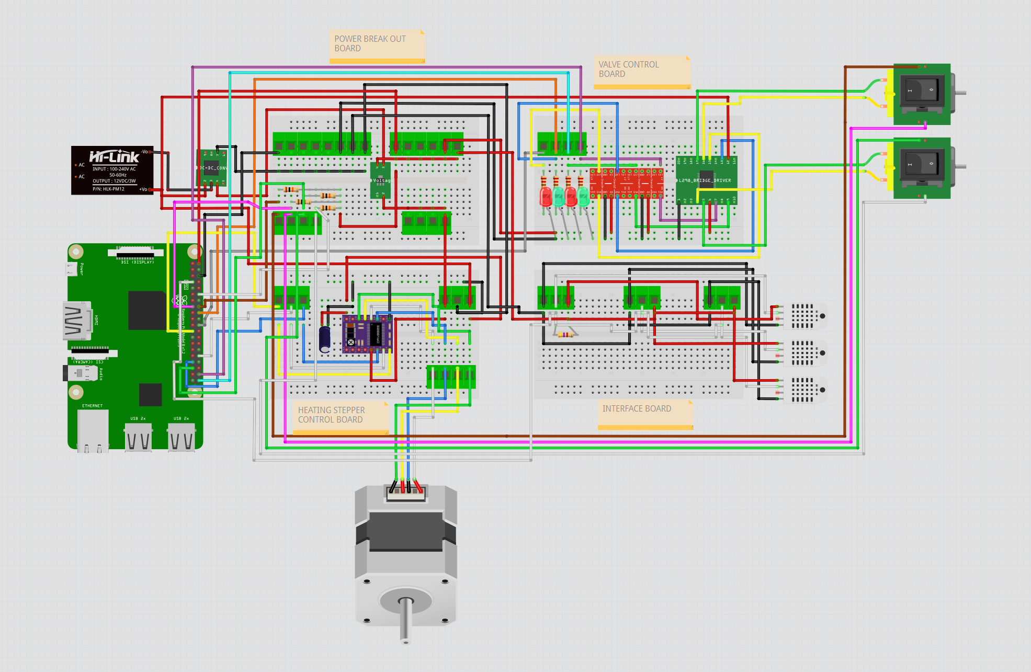
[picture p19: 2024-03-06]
Diagrams/Prototype Controller System/Still-Controller-and-Monitor-Schematic.png

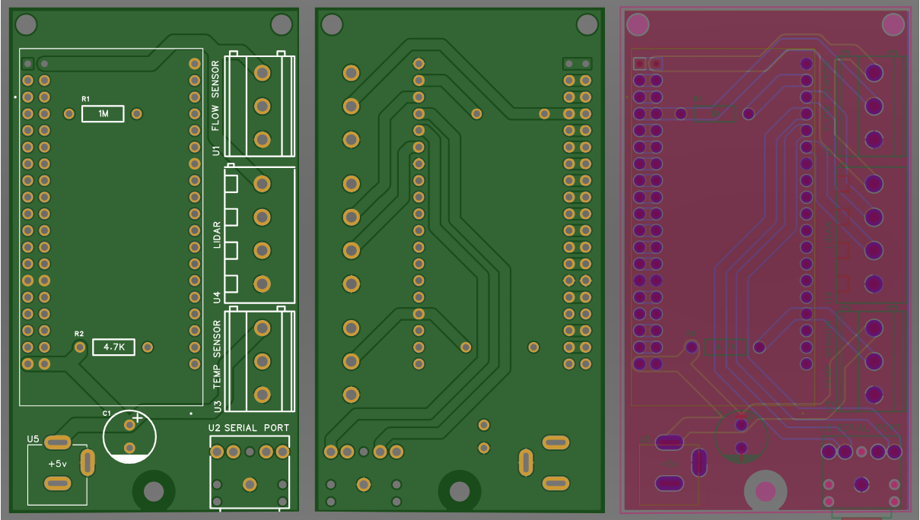
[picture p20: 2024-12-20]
Diagrams/LIDAR Hydrometer Reader/Bird-Brain-PCB.png

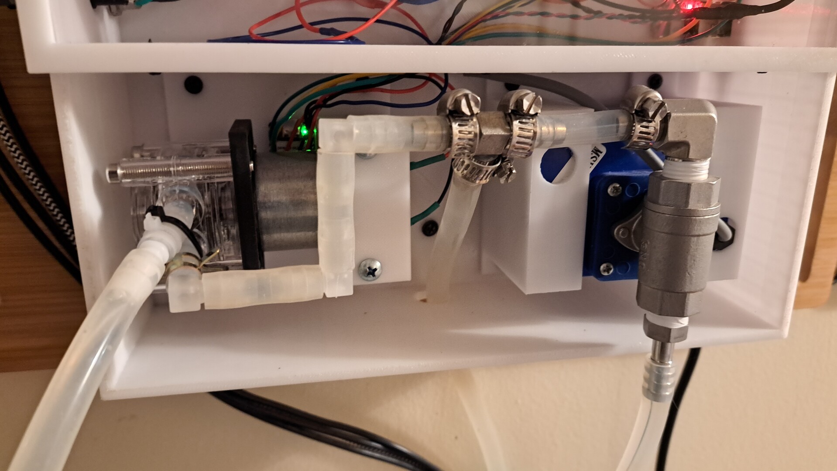
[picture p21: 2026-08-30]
Diagrams/Dephleg Driver/Dephleg Driver 3.jpg

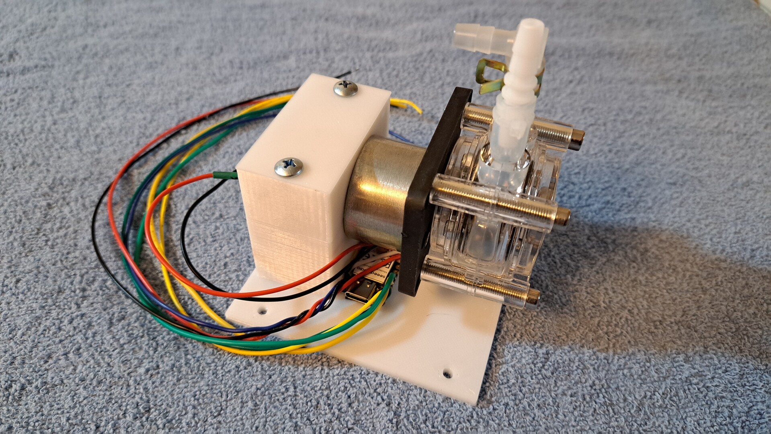
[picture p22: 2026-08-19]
Diagrams/Dephleg Driver/Dephleg Driver 2.jpg

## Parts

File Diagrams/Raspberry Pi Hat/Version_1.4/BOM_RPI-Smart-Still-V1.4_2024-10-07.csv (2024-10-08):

ID | Name | Designator | Footprint | Quantity | Manufacturer Part | Manufacturer | Supplier | Supplier Part | Price
1 | 470uF 35v | C1,C2 | CAP 35V 470UF | 2 | KMG35VB470M10*16 LO | SAMYOUNG(韩国三莹) | LCSC | C165500 | 0.187
2 | 470uF 16V | C3 | 470UF 16V AMIR | 1 | 470uf16v | ValuePro | LCSC | C28067 | 0.03
3 | 1N4148 | D9,D10 | DO-35_BD2.0-L4.0-P8.00-D0.5-FD | 2 | 1N4148 | SEMTECH | LCSC | C14516 | 0.007
4 | MINI BLADE FUSE +5v | F1 | AMAZON MINI BLADE FUSE HOLDER | 1 |  |  |  | SL-506P
5 | MINI BLADE FUSE +12/24v | F2 | AMAZON MINI BLADE FUSE HOLDER | 1 |  |  |  | SL-506P
6 | LED0603-GREEN | GPIO17-ON/OFF,GPIO27-ON/OFF,VALVE1_CLOSE,VALVE1_OPEN,VALVE2-CLOSE,VALVE2-OPEN | LED-TH_BD3.0-P2.54-RD-RED | 6 | OP265B | OPTEK | LCSC | C6346513 | 2.796
7 | KF129-5.08-4P | J1,J2,J3 | CONN-TH_4P-P5.08_KF129-5.08-4P | 3 |  | null | LCSC | C9900018789
8 | 2N3904(TO-92) | Q1,Q2 | TO-92-3_L5.1-W4.1-P1.27-L | 2 | 2N3904 | SEMTECH | LCSC | C118538 | 0.016
9 | 10kΩ | R1,R2,R3,R7 | RES-TH_BD2.4-L6.3-P10.30-D0.6 | 4 | MFR50SFTE52-1K | YAGEO(国巨) | LCSC | C173143 | 0.019
10 | 4.7kΩ | R6 | RES-TH_BD2.4-L6.3-P10.30-D0.6 | 1 | MFR50SFTE52-1K | YAGEO(国巨) | LCSC | C173143 | 0.019
11 | 1kΩ | R8,R9,R14,R15 | RES-TH_BD2.4-L6.3-P10.30-D0.6 | 4 | MFR50SFTE52-1K | YAGEO(国巨) | LCSC | C173143 | 0.019
12 | 220Ω | R11,R12,R13,R16 | RES-TH_BD2.4-L6.3-P10.30-D0.6 | 4 | MFR50SFTE52-1K | YAGEO(国巨) | LCSC | C173143 | 0.019
13 | SRD-05VDC-SL-C | RLY1,RLY2 | RELAY-TH_SRD-XXVDC-XL-C | 2 |  | 松乐 | LCSC | C35449 | 0.318
14 | KF129-5.08-2P | U1,U4,U6 | CONN-TH_P5.08_KF129-5.08-2P | 3 |  | KEFA(科发) | LCSC | C475092 | 0.183
15 | L298N_Module | U2 | L298N_MODULE | 1 | L298N
16 | KF129-5.08-3P | U3,U8 | CONN-TH_3P-P5.08_KF129-5.08-3P | 2 | KF129-5.08-3P | KEFA(科发) | LCSC | C475093 | 0.284
17 | HDR_RPI_HAT | U7 | HDR-TH_40P-P2.54-V-F-R2-C20_2202992 | 1
18 | Buck Converter 6V-27V-->5V | U9 | BUCKCONVERTER5V | 1 |  | OFO Tech Sdn Bhd
19 | TC040125-220M-UL | U10 | IND-TH_L13.2-W7.5-P6.00-D0.7 | 1 | TC040125-220M-UL | SXN(顺翔诺) | LCSC | C5244123 | 0.117
20 | IIC I2C Logic Level Converter Bi-directional 5V to 3V3 | U13,U16 | IIC I2C LOGIC LEVEL MODULE | 2
21 | A4988 | U15 | DRV8825 | 1

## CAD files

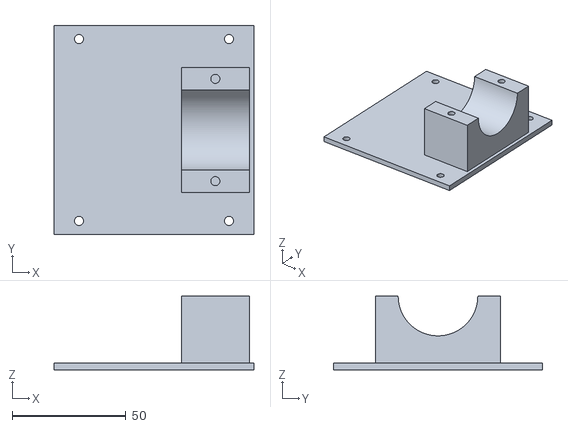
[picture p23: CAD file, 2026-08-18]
3D-Models/Controller Case/DD-Pump-Base.stl
88.0 x 92.0 x 32.5

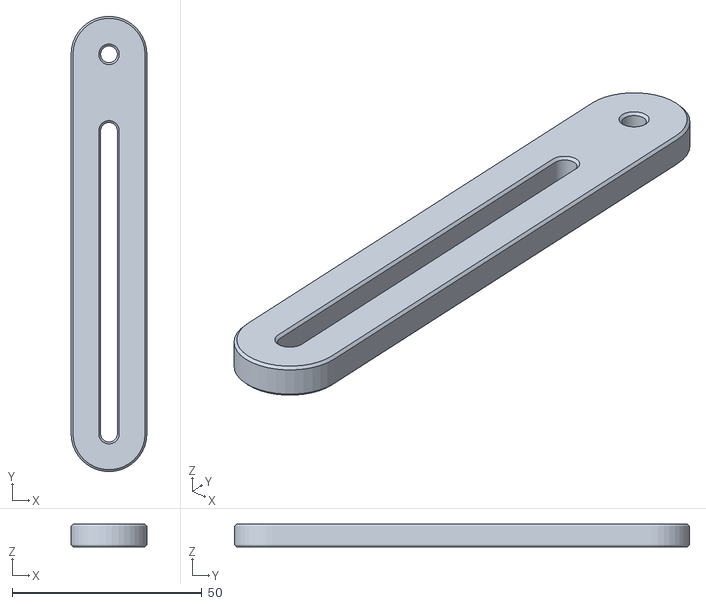
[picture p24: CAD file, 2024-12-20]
3D-Models/LIDAR Hydrometer Reader/34-Copper-flow-Sensor/Flow Sensor Mount/arm4.stl
20.0 x 119.9 x 6.00

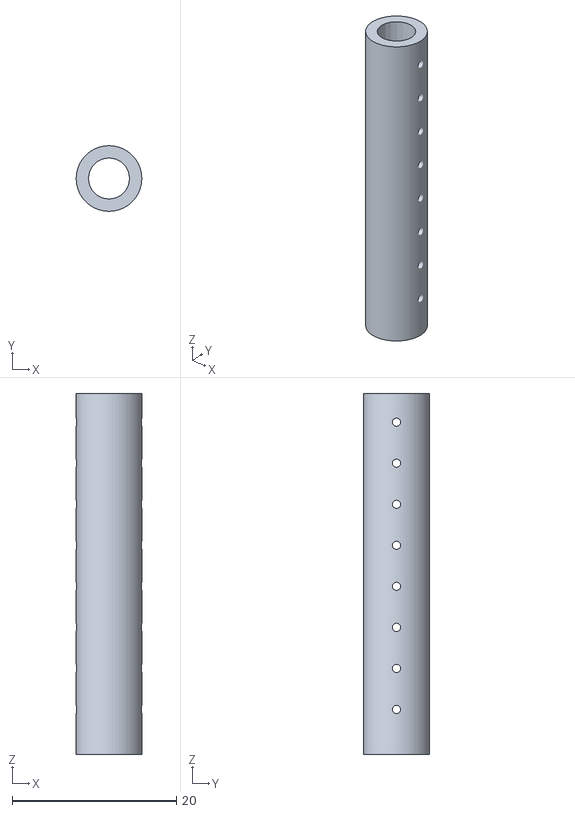
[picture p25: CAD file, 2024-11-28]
3D-Models/LIDAR Hydrometer Reader/34-Copper-flow-Sensor/Flow Sensor Overflow Sleeve.stl
8.00 x 8.00 x 44.0

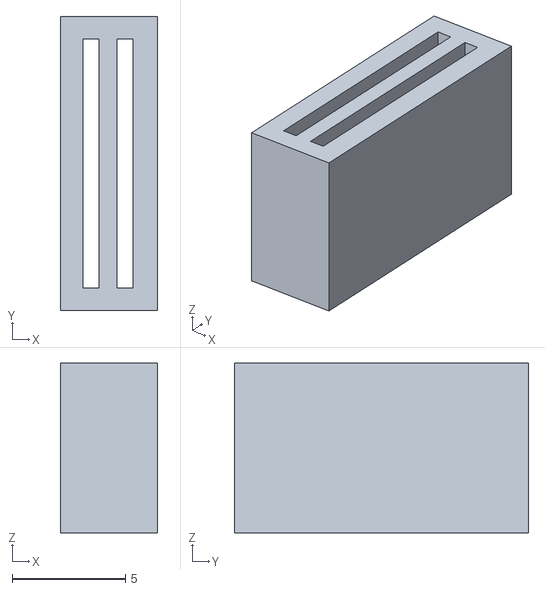
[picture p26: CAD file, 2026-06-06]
3D-Models/LIDAR Hydrometer Reader/Flow-Sensor-Plate-Spacer.stl
4.30 x 13.0 x 7.50

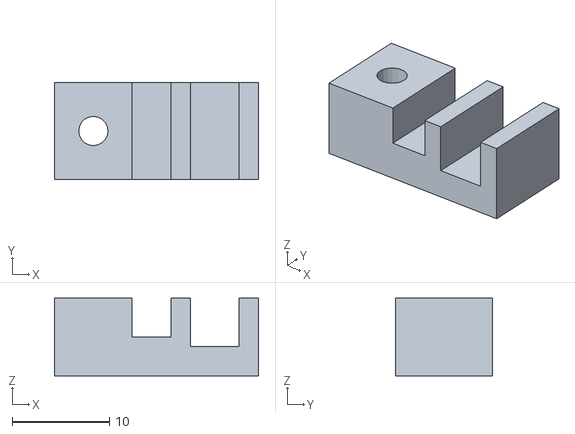
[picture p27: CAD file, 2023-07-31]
3D-Models/Misc/Dual Cable Guide.stl
21.0 x 10.0 x 8.00

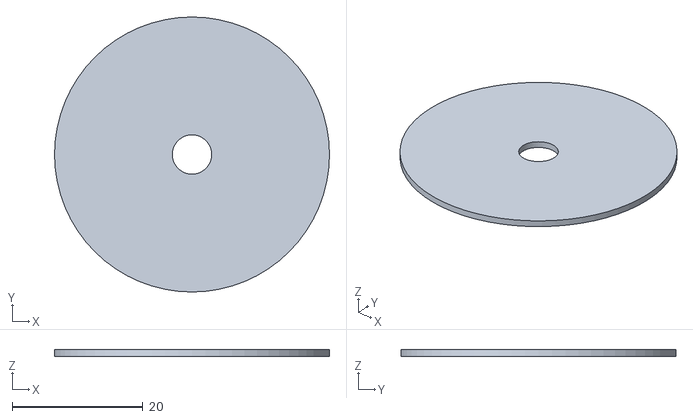
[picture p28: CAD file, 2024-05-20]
3D-Models/Prototype Projects/LIDAR Hydrometer Reader/LIDAR Hydrometer Reflector Template.stl
42.0 x 42.0 x 1.00

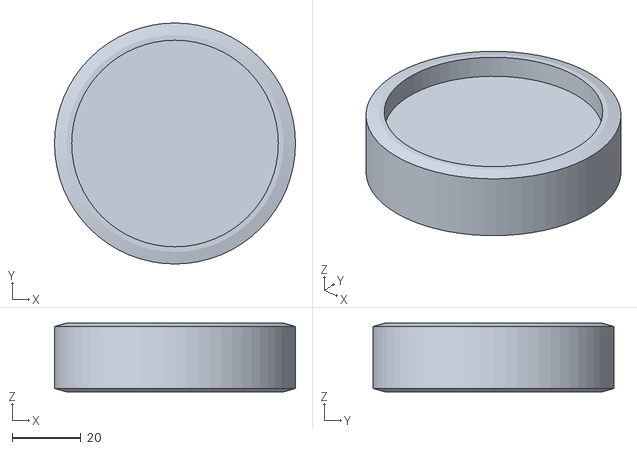
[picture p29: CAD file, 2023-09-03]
3D-Models/Prototype Projects/Load Cell Hydrometer/Parrot Cup Base.stl
70.0 x 70.0 x 20.0

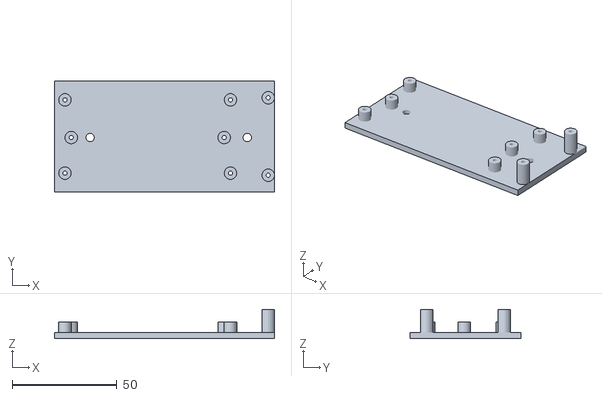
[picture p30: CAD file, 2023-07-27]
3D-Models/Prototype Projects/RPi Smart Still/Valve Controller Mounting Plate.stl
105.0 x 53.0 x 14.0

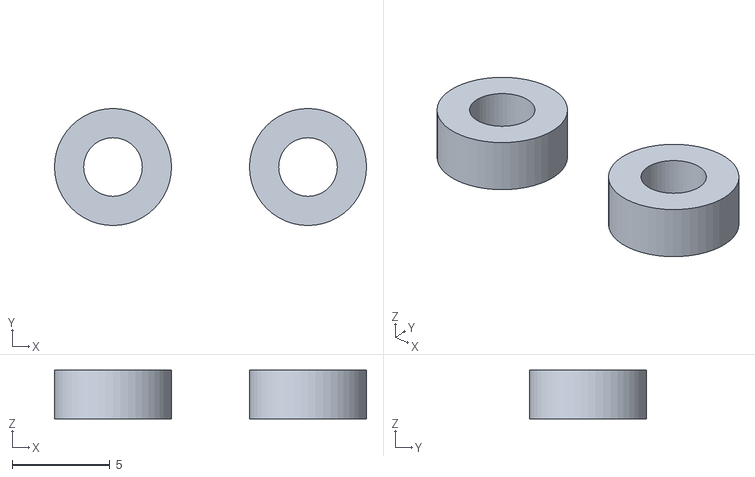
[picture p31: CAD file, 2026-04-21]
3D-Models/Raspberry Pi Hat/RPi + Hat + DRV Spacers.stl
16.0 x 6.00 x 2.50

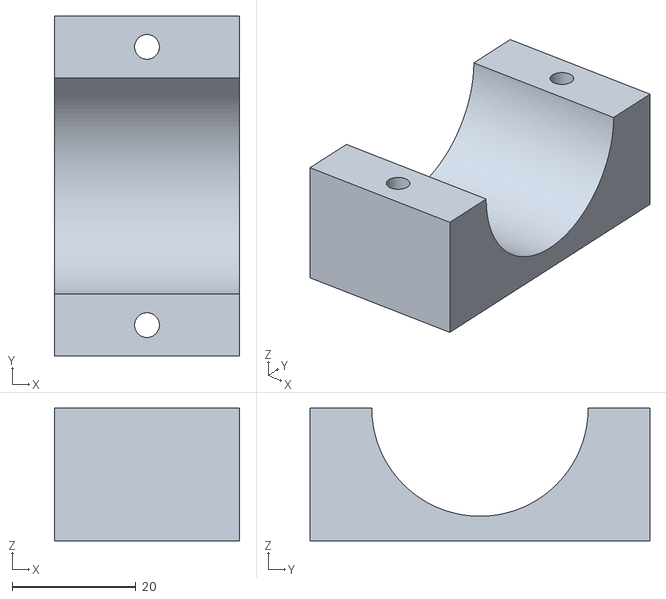
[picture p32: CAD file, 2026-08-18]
3D-Models/Controller Case/DD-Pump-Clamp.stl
30.0 x 55.0 x 21.5

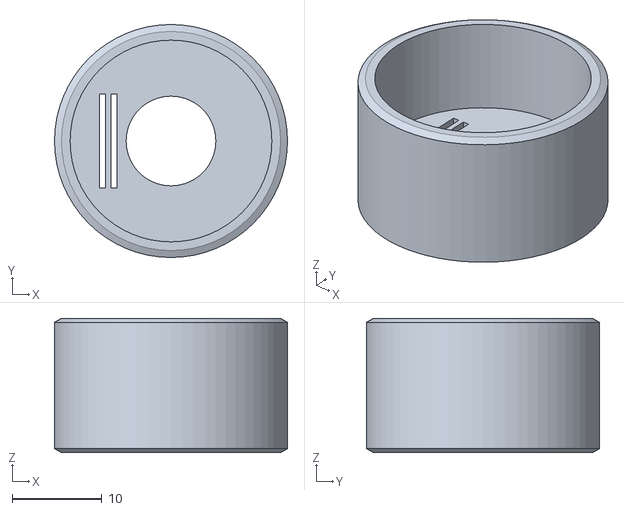
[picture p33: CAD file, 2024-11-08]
3D-Models/LIDAR Hydrometer Reader/34-Copper-flow-Sensor/Flow Sensor Cap.stl
26.0 x 26.0 x 15.0

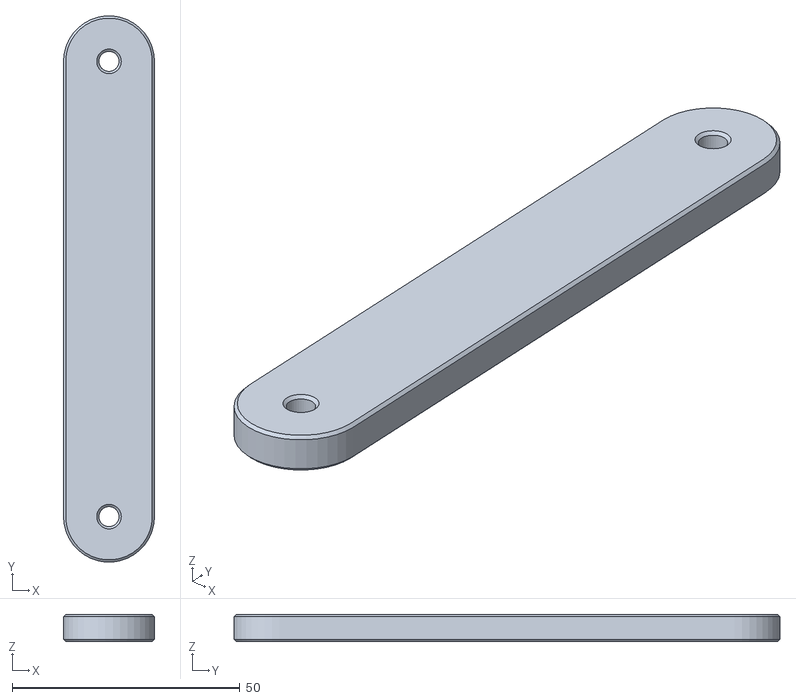
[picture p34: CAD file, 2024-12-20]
3D-Models/LIDAR Hydrometer Reader/34-Copper-flow-Sensor/Flow Sensor Mount/arm3.stl
20.0 x 119.9 x 6.00

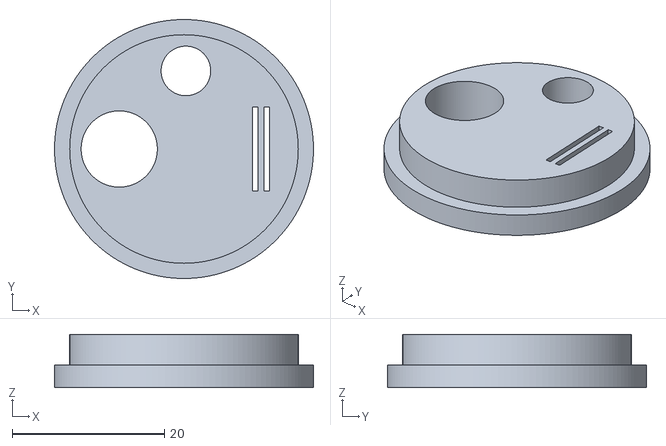
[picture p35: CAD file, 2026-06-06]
3D-Models/LIDAR Hydrometer Reader/Flow-Sensor-Cap.stl
34.0 x 34.0 x 7.00

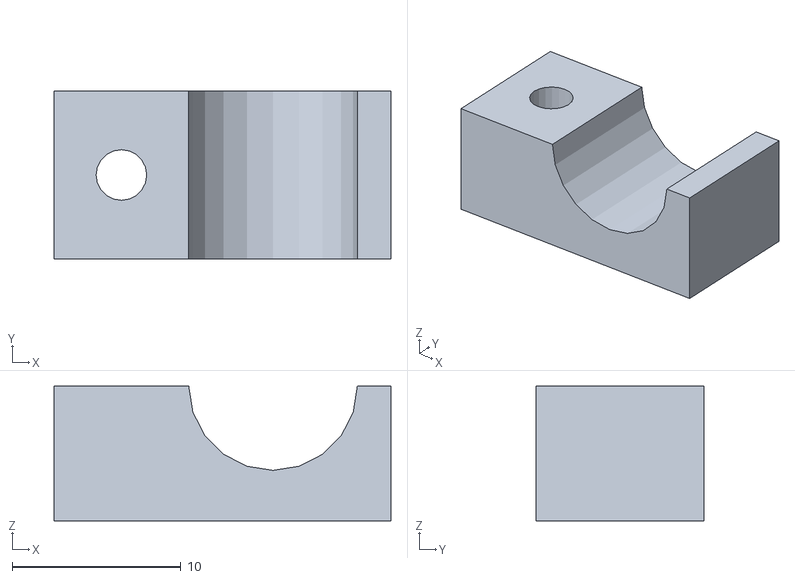
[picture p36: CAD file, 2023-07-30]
3D-Models/Misc/10mm Half Tunnel Wire Guide.stl
20.0 x 10.0 x 8.00

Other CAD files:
3D-Models/Prototype Projects/LIDAR Hydrometer Reader/LIDAR Sensor Mount.stl
3D-Models/Prototype Projects/Load Cell Hydrometer/Flow Sensor Wheel.stl
3D-Models/Prototype Projects/RPi Smart Still/Power Breakout Mounting Plate.stl
3D-Models/Raspberry Pi Hat/RPi + Hat Mounting Plate (Tall).stl
3D-Models/Controller Case/RPi-SS-Case-Bottom.stl
3D-Models/Controller Case/RPi-SS-Case-Cover.stl
3D-Models/Controller Case/RPi-SS-Cover-Frame.stl
3D-Models/Controller Case/RPi-SS-Fan-Cover.stl
3D-Models/Controller Case/RPi-SS-Servo-Valve-Mount.stl
3D-Models/LIDAR Hydrometer Reader/34-Copper-flow-Sensor/Flow Sensor Mount/0.75-Pipe clamp-Half-1.stl
3D-Models/LIDAR Hydrometer Reader/34-Copper-flow-Sensor/Flow Sensor Mount/0.75-Pipe clamp-Half-2.stl
3D-Models/LIDAR Hydrometer Reader/34-Copper-flow-Sensor/Flow Sensor Mount/0.75-Pipe clamp-v1.3.stl
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

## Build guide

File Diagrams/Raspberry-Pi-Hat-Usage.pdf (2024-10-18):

## Raspberry Pi Hat Usage

Thanks to Mathias at Firefly3D in Sweden, the RPi Smart Still controller system is nowhere near as complicated to build as the original prototype system. Whether you build the Raspberry Pi Hat boards yourself, or order them already assembled, there are still quite a few wires connected to them. But, this is still easier to build because all you need is a screwdriver to assemble a system.

Below is an image of the Raspberry Pi Hat printed circuit board with everything blurred out except for the screw terminal locations. This is so I can easier explain what all of the screw terminals are for and what connects to each one.

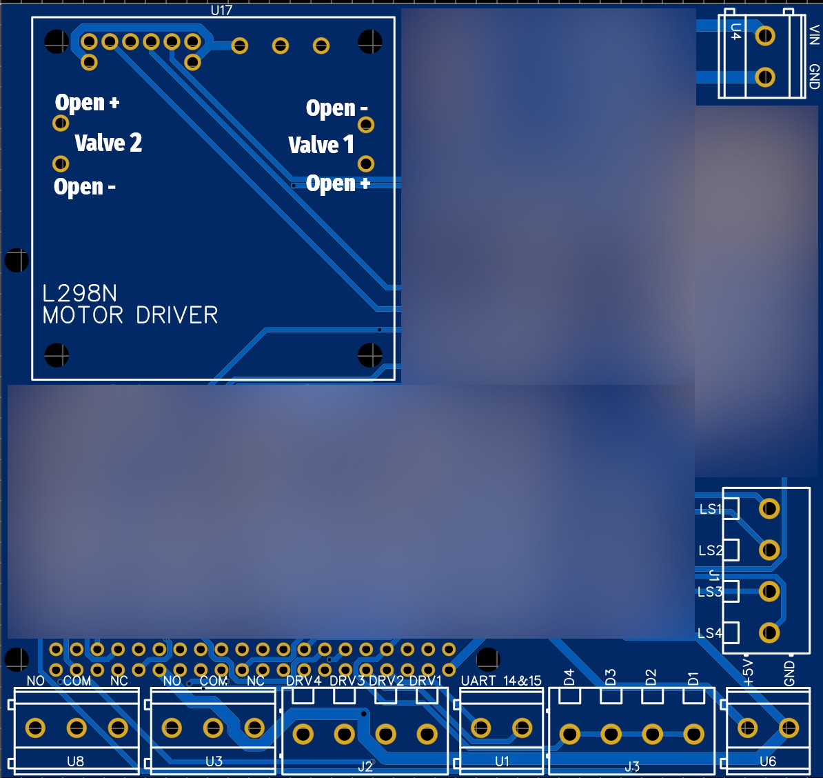
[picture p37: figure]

U4: In the upper right corner, this is where the power supply connects. Unlike the prototype system, the Raspberry Pi Hat based system only runs on 12 volts. After some testing with the prototype system, I was able to determine that running one on 19 to 24 volts really isn’t best. The cooling valves actually move a little too fast and this affects the ability to automatically dial in dephlegmator settings. A simple 12 volt, 5 amp power brick is all that’s needed. These are available on Amazon all day long, every day, from numerous sellers.

L298N MOTOR DRIVER: This is the footprint where the motor driver board for the cooling valves is situated. If you look at the assembled hats that I sell on my website (https://panhandleponics.com) (https://panhandleponics.com/rpi-smart-still-controller-components/) you will notice that I modify these motor driver boards so they simply plug into a socket on the hat. So all we need to be concerned with here are the 2-conductor screw terminals on the board that I’ve labeled as Valve 1 (condenser) and Valve 2 (dephlegmator). If you are using the same US Solid brand valves (https://www.amazon.com/gp/product/B06Y16BDFG/) that I use (covered in the Still-Monitor-and-Controller (https://github.com/larry-athey/rpi-smart-still/blob/main/Diagrams/Prototype-System/Still-Monitor-and-Controller.pdf) document) the blue wires are the Open + and the yellow wires are the Open -.

U8 and U3: These are the switching terminals for auxiliary relays 1 (U3) and 2 (U8). These should only be used for switching low voltage, low current loads. DO NOT use these for switching AC powered loads. If you need to switch AC loads, you should use these relays to switch remote solid state relays mounted as close to the AC load as possible. Every solid state relay that I’ve ever seen, uses a 3 to 32 volt DC signal, so you could just as easily use the 12 volts from your existing power brick here. The terminals from left to right are normally closed, common, and normally open. The contacts on these relays are only rated at 10 amps, so you should really avoid anything over 5 amps to avoid contact burn/sparking.

J2: This is the connector for the stepper motor that runs your heating dial. Hats that I sell on my website are pre-adjusted to work with a Nema 17 motor (https://www.amazon.com/gp/product/B088BLQYDX/) (.540 volts on the current limiter) which I use to run the potentiometer on an SCR based power controller. (https://www.amazon.com/gp/product/B0BF9X63XZ/) If you are using any kind of a gas burner, you will want a gear drive stepper motor (https://www.amazon.com/STEPPERONLINE-Planetary-Gearbox-Stepper-Printer/dp/B00WATUFIG/) due to the added torque required to turn a gas valve. The terminals here are for the pair of coils of the stepper motor (1a, 1b, 2a, 2b). If the motor appears to run in reverse, you can either switch the coils here, or invert the stepper rotation in the user interface under the Configure Heating section.

U1: This is the serial data connection for the digital hydrometer. Keep in mind that in serial communications, the TX line from one device always connects to the RX line of the other device. The left terminal is the Raspberry Pi TX line, and the right terminal is the RX line. In the LIDAR hydrometer readers that I sell on my website, the tip of the 3.5mm audio cable is its TX line, the ring is the RX line. Obviously, the ground of the plug connects to the hat’s ground.

J3: This is the bus for the DS18B20 temperature sensor data lines. Yes, there are only 3 used by the system at this time, but an extra terminal was added here to fill in the empty space. It doesn’t matter which sensor is connected to which terminal here. These are 1-Wire Network devices and all share the same GPIO pin on the Raspberry Pi.

U6: This is the 5 volt power supply output used for powering various other parts of the system. Such as the DS18B20 temperature sensors, the power supply for the digital hydrometer, and anything else you need to power. Keep in mind that this has a 5 amp current limit. I generally suggest connecting these two terminals to screw terminal strips to make it easier to connect these extra devices. You will have 3 grounds for the temperature sensors, 2 for the valve limit switches, and 2 for the digital hydrometer (one for power and one for serial data).

J1: These are the terminals for the valve limit switches. If you are using the same US Solid brand valves (https://www.amazon.com/gp/product/B06Y16BDFG/) that I use, the limit switches are on the red and green wires, red is the closed limit, green is the open limit. LS1 is the Valve 1 open limit, LS2 is the Valve 1 closed limit, LS3 is the Valve 2 open limit, and LS4 is the Valve 2 closed limit. The way the limit switches work is that when either of the terminals are grounded, the valve is at its limit in that direction. If neither are grounded, the valve is somewhere in between. The position is tracked by knowing how many milliseconds has been applied to the motor in either direction. This isn’t dead on accurate, but it doesn’t need to be and things are always reset whenever either of the limit switches shorts to ground.

That covers all of the connections to the Raspberry Pi Hat. Please refer to the Still-Monitor-and-Controller (https://github.com/larry-athey/rpi-smart-still/blob/main/Diagrams/Still-Monitor-and-Controller.pdf) document for further information. Understanding things in the original prototype design will help you understand what the hat is doing. This document also contains Amazon links to various parts and accessories you might need for your system build.

All future videos that I upload on the RPi Smart Still controller system will be on my new system based on the Raspberry Pi Hat. I have cannibalized my prototype system for parts, so it officially no longer exists and I really don’t see any point in providing support for builds based on that system any further.

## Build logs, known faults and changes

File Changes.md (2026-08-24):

Changes since the version 1.04 release

---

- Created a completely 3D printable system case that simplifies complete builds and caters to both headless and fully self-contained builds with local screen/tablet interfaces.

- A new optional accessory has been added called the [Dephleg Driver](https://github.com/larry-athey/rpi-smart-still/tree/main/Dephleg-Driver) that replaces the dephleg cooling water valve. This was added after a number of people notified me that they use recirculating cooling water tanks running on impeller driven pond pumps which don't provide enough pressure to keep water flowing when the valve is at 30% or lower.

- LIDAR Hydrometer Reader code updates that simplify the calibration and improves the accuracy by implementing temperature compensation and scientific scale measurement translation.

- All undercarriage timing parameters are now configurable from a new **Configure Tuning** page added to the management menu. This allows precision tuning of the controller system to the still that it's attached to.

- Improved Boilermaker API integration which allows the system to run the Boilermaker more like a digital SCR controller. As in, the boiler temperature is allowed to naturally rise over time, but is more precisely controlled within the preset window.

- Boilermaker fallback power setting is now a per-program parameter since different power levels are needed based on whether a reflux mode or pot still run is being performed. Previously, the Boilermaker's internal fallback power setting was used.

- Dephleg cooling valve management routines optimized and simplified to make things more accurate with far fewer steps.

- Improved valve synchronization at distillation run startup and pause/resume to compensate for potential mechanical play/slop issues which is common in the cheap US Solid style knock-offs.

- Heating stepper motor control updated to use 5% of total motor steps rather than using the 10% heat-jump positions for boiler temperature management during a distillation run. This is so stepper motor heating control is more like Boilermaker operation.

- Two major bugs fixed in the timeline rendering that were preventing flow sensor and Boilermaker power level readings from displaying.

- Numerous user interface tweaks and bug fixes, more touch-screen friendly now.

- A new page has been added to the Wiki that covers all of the [configuration settings](https://github.com/larry-athey/rpi-smart-still/wiki/13.-Configuration-Settings) in the management menu. It seems that there are some people who prefer to print manuals rather than watching how-to videos.

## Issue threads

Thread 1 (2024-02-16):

Access denied

FireflySE, 2024-02-16:
Hi

I completed the installation successfully but getting this message in browser.
I guess its a permission issue but where do I start?

Warning: mysqli_connect(): (HY000/1698): Access denied for user 'rssdbuser'@'localhost' in /var/www/html/index.php on line 84

Warning: mysqli_query() expects parameter 1 to be mysqli, bool given in /var/www/html/index.php on line 85

Warning: mysqli_num_rows() expects parameter 1 to be mysqli_result, null given in /var/www/html/index.php on line 86

System settings record is missing, reinstall system from GitHub clone.

Warning: mysqli_close() expects parameter 1 to be mysqli, bool given in /var/www/html/index.php on line 102

larry-athey, 2024-02-16:
The error says that the system settings record is missing from the database. Do any of the database tables exist? You can log into PhpMyAdmin (http://[your-pi-ip]/phpmyadmin) using the database credentials found at the top of subs.php and look at the database.

You can always run the install.sh script again and watch your screen for any errors.

FireflySE, 2024-02-16:
Hi

Thanks for the reply :)

I managed to set new password for root in safe mode so now I can access MariaDB at least.
I have databases as shown below. I will check subs.php if i can find it...

MariaDB [(none)]> show databases;
+--------------------+
| Database           |
+--------------------+
| information_schema |
| mysql              |
| performance_schema |
| phpmyadmin         |
+--------------------+
4 rows in set (0,023 sec)

MariaDB [(none)]>

larry-athey, 2024-02-16:
See line 75 of install.sh, that's where the database for the system is created. If you run the script again, you should be seeing an error if that step is failing. Obviously, it failed, or you would have a database named "rpismartstill" in your list.

larry-athey, 2024-02-17:
I'm a bit baffled by what you said about setting a new root password. The part of the install script that secures the MySQL (mariadb) installation removes the root password. You can just use `sudo mysql` to get a command line.

Are you not using a stock unaltered Raspbian installation as the wiki suggests?

FireflySE, 2024-02-17:
Yes I used a fresh install of latest 32bit debian legacy with desktop on my raspberry 3. I did not update before installation either. Also after installation bluetooth disappear so have to use VNC from my PC. Tried to connect to mysql but access denied the same as the browser message says. But something as you say must go wrong with installation because of the missing database I will make a new fresh install and pay more attention for errors.

FireflySE, 2024-02-17:
I manage to see one error during installation "error unable to GET" but it disappears so fast and installation continues... Is there a log file some where? I checked again and the database is not installed. When installing MariaDB and phpmyadmin does it matter what I choose there or should it work either way?

Br

larry-athey, 2024-02-17:
The log would be your terminal buffer, you just scroll the window backwards. You can also redirect the output of the script to a text file in order to create a log file by running `install.sh > install.log  2>&1`

larry-athey, 2024-02-17:
Please pull the code tree again and re-run install.sh

```
You can delete this git clone after you are done, it is no longer needed.

pi@test-pi:~/rpi-smart-still/Undercarriage $ sudo mysql
Welcome to the MariaDB monitor.  Commands end with ; or \g.
Your MariaDB connection id is 62
Server version: 10.5.23-MariaDB-0+deb11u1 Raspbian 11

Copyright (c) 2000, 2018, Oracle, MariaDB Corporation Ab and others.

Type 'help;' or '\h' for help. Type '\c' to clear the current input statement.

MariaDB [(none)]> show databases;
+--------------------+
| Database           |
+--------------------+
| information_schema |
| mysql              |
| performance_schema |
| phpmyadmin         |
| rpismartstill      |
+--------------------+
5 rows in set (0.001 sec)

MariaDB [(none)]>
```

FireflySE, 2024-02-17:
Thanks I will make another try tomorrow I get back to you with the result

FireflySE, 2024-02-18:
pi@raspberrypi:~ $ sudo mysql
Welcome to the MariaDB monitor.  Commands end with ; or \g.
Your MariaDB connection id is 40
Server version: 10.5.23-MariaDB-0+deb11u1 Raspbian 11

Copyright (c) 2000, 2018, Oracle, MariaDB Corporation Ab and others.

Type 'help;' or '\h' for help. Type '\c' to clear the current input statement.

MariaDB [(none)]> show databases;
+--------------------+
| Database           |
+--------------------+
| information_schema |
| mysql              |
| performance_schema |
| phpmyadmin         |
+--------------------+
4 rows in set (0.002 sec)

MariaDB [(none)]>

FireflySE, 2024-02-18:
This is what the log file shows

^[[H^[[2J^[[3JTHIS INSTALLER EXPECTS YOU TO BE USING A RAW UNMODIFIED OS INSTAL>

If you are using anything prior to a Raspberry Pi 4, you need to be running
a 32 bit version of Raspbian, even though there are 64 bit versions for it.
Unless you have 4+ GB of RAM, a 64 bit OS is completely useless. You surely
will have problems compiling the servo valve driver under a 64 bit Raspbian
on anything older than a Pi 4.

Press ENTER to continue the installation or CTRL+C to cancel...^[[?1049h^[[22;0>
^[[K
^[[K
^[[K
^[[K
^[[K
^[[K
^[[K
^[[K
^[[K
^[[K
^[[K^[[1;1H^[[37mPackage configuration^[[3;2H^[[30m^[[47m┌─────────────────────>

larry-athey, 2024-02-18:
You didn't pull a fresh copy of the code. I can tell by the message at the beginning of the installation, it's missing a complete paragraph.

FireflySE, 2024-02-18:
I deleted old clone and downloaded it again and now out of the blue the database appeared apparently the 4th time is the charm ;) and I can access via web browser so thank you so much.

FireflySE, 2024-02-18:
Is there a config file for configure gpio pins etc?
I have an electric heater so need to do some adjustment to the code and GUI.

larry-athey, 2024-02-18:
This is all still pre-release. As you can see, there isn't even a first release version showing on the GitHub page. I'm slowly working on the PDF files in /Diagrams/ as I get free time. Until then, you have to refer to the source code. You will need to do regular code syncs until there is an official first release because things are updated here as I make changes on my end.

FireflySE, 2024-02-18:
Then thank you for all the help and your hard work. Looking forward for the future of rpi smart still

Br

Closed 2024-02-18.

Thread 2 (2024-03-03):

Schematic overview

FireflySE, 2024-03-03:
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

Sorry for all the mess I tried to follow your instructions and made a schematic for the hole system except the scr and heating element.
If you have the time please look it over and give me input.

FireflySE, 2024-03-03:
[RPI Smart Still.zip](https://github.com/larry-athey/rpi-smart-still/files/14473486/RPI.Smart.Still.zip)
Puting the fritzing file here as well

larry-athey, 2024-03-03:
Thanks! You obviously have way more patience for that Fritzing program than I have. I think it's because their parts library doesn't contain all the parts that I use. Does Fritzing have a way to use the schematic in order export a Gerber file that could be used to make printed circuit boards?

FireflySE, 2024-03-03:
Yes its not that good you have to improvise..  I think EasyEDA is better, but for this project and because the breadboard overview its easy to follow. I wanted to contribute with something to the project at least. I haven´t used Fritzing that much either so to export to a gerber file a guess that´s possible but I would use a better software for that. My plan for the future is to make a gerber and order a nice pcb but for now I want to test and play with your fine project.

larry-athey, 2024-03-04:
Everything looks correct to me. I'd like to put these in the /Diagrams/ folder here and create a README.md to describe what's what. How do you want me to credit you for these? FireflySE or some other name?

Also, I just pushed an update so you will want to sync your code again. I discovered an oversight in the process.php that saves the DS18B20 sensor addresses.

FireflySE, 2024-03-04:
FireflySE is fine thank you. And will sync the code 👍

FireflySE, 2024-03-04:
oh as you see on the schematic i used 12v system if you want to change it to 24v please do.

FireflySE, 2024-03-04:
Updated schematic missed power and ground to one of the logic level shifters

FireflySE, 2024-03-08:
Hi, couldn´t help it I made a prototype pcb with some extra features it needs to be verified but this is my take on a HAT module.
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

FireflySE, 2024-03-08:
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

larry-athey, 2024-03-08:
What are the extra features, and what is the long J1 connector for?

FireflySE, 2024-03-09:
The 2 relays is in my case for controlling 2 12v water pumps. There are 2 3pin screw connectors on the board for this.
Then i added led fault and power indicators.

FireflySE, 2024-03-10:
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
Updated layout, smaller board 100x90 and 4 layers.

FireflySE, 2024-03-11:
Updated with more common components and footprints
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

FireflySE, 2024-03-11:
New update with more common components and footprints. I will order the first prototype and let you know how it goes.
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

larry-athey, 2024-03-12:
What's your plan for connecting the temperature sensors?

FireflySE, 2024-03-12:
Good point they need 5v and ground according to your schematic I missed this and should be 4.7k resistors on the data line I have corrected this now. Thanks for the observation

FireflySE, 2024-03-12:
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

FireflySE, 2024-03-12:
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

FireflySE, 2024-03-12:
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

larry-athey, 2024-03-12:
Oh, I just figured you had some other kind of external device planned to connect them and the serial lines to J1.

FireflySE, 2024-03-13:
Aaah ok yes that make sense will update the schematic.

FireflySE, 2024-03-13:
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

FireflySE, 2024-03-13:
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

FireflySE, 2024-03-13:
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

FireflySE, 2024-03-13:
Nice thanks I added an extra connection only for if you want an extra sensor somewhere but maybe its unnecessary..

FireflySE, 2024-03-15:
I think I am done tinkering with the board now and ready to order a prototype. Will let you know how much magic smoke I got ;)

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

larry-athey, 2024-03-16:
Wow, I'm guessing that this was all done in EasyEDA. I have yet to give that a try, I just haven't had the time to mess with it. I can see that you've driven completely around the use of the modules that I use and duplicated them right on the PCB. That's probably another reason why I haven't tried working with it, I'm still not sure of the lifespan of them so I'm still hung up on using things that can be replaced at the modular level.

Let me know if it keeps all of the magic smoke inside! LOL!!!

FireflySE, 2024-03-16:
Yes I used EasyEda for this, because of low use hours if you destill on hobby basis I hope it will last a long time. But I will check temperature of components and make necessary adjustments if need be. The cost of the board at jlcpcb is 7$ for me to get it to Sweden about 20$. If it works as intended without too much magic smoke I will upload the gerber file. 🤣

larry-athey, 2024-05-04:
Just checking in to see what the status is on the PCB. I also wanted to ask if I'm overlooking the serial connector for the hydrometer data communications. I'm in the middle of building a simplified alternative that uses LIDAR to read the floating height of a glass hydrometer in a normal parrot. It will still have the temperature sensor on the input, but the flow sensor will be moved to the parrot output.

FireflySE, 2024-05-04:
Hi,
Interesting project similar to what George D. did if I recall correctly. I have been way to busy with work unfortunately. The test pcb have arrived I assembled the pcb but it shorts out some where "no smoke"😉 have not yet been been able to test it further. I only noticed that the drv8825 ic got warm. I can send you the gerber file if you want to take a look. What do you mean by overlooking serial connection?
I cant see what could cause it to not work with current setup🤔

br Mathias

larry-athey, 2024-05-05:
I was referring to the two UART pins 14 and 15 on the GPIO bus, that's how the PI and the hydrometer talk to each other.

George's "talking parrot head" uses the same type of sensor, but that PVC tube on top of the parrot is entirely too bulky. You can do the same thing with the sensor attached to the side of the parrot aiming upward and not make it top heavy. Mine also has the flow sensor on the output of the parrot and the temperature sensor on the input side. This will be easier to build and calibrate, I spooked too many people with the load cell based digital hydrometer.

FireflySE, 2024-05-05:
Ok yes I have not added a separate connector for 14-15 and you're right that would be nice to have on the board. I can add this to the next test pcb. They are on the rpi output pins on my schematic.

I agree your solution is better 👍, But I fell in love with your loadcell solution so I think i will use that but nice to have options.

I work with EBF 3D printing and we are in the works with building a new industrial machine and we work alot even weekends so sorry for not being fast to respond. If your interested take a look at www.freemelt.com.

Br Mathias

larry-athey, 2024-05-06:
I wish there were companies like that around here, I'd love to have a job in that type of industry.

FireflySE, 2024-05-07:
Iam sorry to hear that.. We actually have a branch on US soil now and we hope to expand with the new "america makes" investment.

Keep in touch

Br Mathias

larry-athey, 2024-05-11:
Those relays you added to GPIO 17 and 27...Should I send those pins high at the start of a run and then low at the end? Or are you implementing something else to control them?

FireflySE, 2024-05-11:
My thought for those were pumps and yes one of them could be high when temp is above maybe 40-45C and above in a normal run. Nr 2 is for reflux and should be high when reflux program is selected. If you dont have controllable valves you can just run 2 pumps was my idea. Could be done with one pump and a manual shut off valve for the reflux. But would be nice to control temp in both condenser and reflux column. If you dont want to add this to your code then its ok 😊

larry-athey, 2024-05-11:
This system would be completely non-functional without the valves and limit switches, the Start Run procedure wouldn't even start if you haven't run the valve calibration routine. Speaking of which, if those relays are for pumps, they would need to be active even if a run isn't active because you need to calibrate the valves under water pressure I've tested the calibration with and without water pressure and the numbers are definitely different.

larry-athey, 2024-05-11:
I'll add a page under the Management menu to toggle them on an off. I can use at least one of them for controlling the power for my water pressure regulator.

FireflySE, 2024-05-11:
Sweet! Is there anything else you want to be added to the board?

larry-athey, 2024-05-11:
No, the serial communications terminals were the only thing that I could see that was needed. I'll be anxious to rebuild my controller with the hat in a smaller form factor.

FireflySE, 2024-05-11:
Ok I will try to figure out the issues soon and send you a functional gerber.Skickat från min Galaxy
-------- Originalmeddelande --------Från: Larry Athey ***@***.***> Datum: 2024-05-11  23:10  (GMT+01:00) Till: larry-athey/rpi-smart-still ***@***.***> Kopia: FireflySE ***@***.***>, Author ***@***.***> Ämne: Re: [larry-athey/rpi-smart-still] Schematic overview (Issue #2)
No, the serial communications terminals were the only thing that I could see that was needed. I'll be anxious to rebuild my controller with the hat in a smaller form factor.

—Reply to this email directly, view it on GitHub, or unsubscribe.You are receiving this because you authored the thread.Message ID: ***@***.***>

larry-athey, 2024-05-12:
OK, the "Control Relays" page is in there and the last on/off state of each relay is restored across reboots.

At this point, I think I'm ready for an official first official GitHub release number of the source code. I intended to have this done by December 31, 2023 but I got my ass kicked by a blizzard that messed up all kinds of my plans. I ran through test distillations of all four of the programs I've included and there wasn't a single issue with any of them.

FireflySE, 2024-05-12:
Nice well done 👍

Closed 2024-10-15.

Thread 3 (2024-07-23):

Using a camera to read the hydrometer?

Mark-Kiwi, 2024-07-23:
Hey Larry! Great work by the way...I've been following this project and have recently purchased a t-500 still with the intention of building your system and give this brewing hobby a go. (It's legal where I'm from).
I noted the change you have made from load cell to the TOF sensor which got me thinking about if there might be any other way to get accurate hydrometer readings....then came up with the brainwave of why not have the RPI read the hydrometer using a camera????
I've seen some projects where people use a RPI and camera and a package called OpenCV to identify objects etc.
Doing more googling I found some instances where people use a camera to measure object sizes, and one where a guy was able to read an dial dial type gauge. Maybe some smart cookie can figure out how to take the actual hydrometer reading. The camera could be mounted in such a position where it's line of sight sits at the top of the parrot so it can identify where the fluid meets the hydrometer. Light levels could be kept constant with some inbuilt lighting...should give a repeatable output and best of all....no moving parts!
It's beyond my skills, but possibly someone out there could figure it out....then it would just be a case of merging it into your system.
The only issue I can think off might be the processing requirements might be too hard on the pi. Would love to hear your thoughts....

larry-athey, 2024-07-23:
The problem with that is that the hydrometer rotates and optical character recognition needs the hydrometer to be oriented so that the numbers are always facing the camera.

Mark-Kiwi, 2024-07-23:
Yeah I had thought about that and came up with two possibile sollutions...
One was to station mirrors either side and behind the hydrometer so the camera has 360 field of view (surely it could be coded to read a reflected/reversed image.)
Or secondly, imagine something like half a vertical tube placed behind the hydrometer and a lightweight horizontal rod attached to the hydrometer. The hydrometer would still be free to move up and down vertically, but if it rotated, the rod would touch the half tube and stop it rotating the scale away from the camera.
:-)

larry-athey, 2024-07-24:
I did a lot of research on this when I first decided to come up with something that was easier for people to build than the load cell hydrometer. I abandoned this idea because it would be even more difficult because of the optics involved and the limitations of the optical character recognition libraries. On top of those limitations, counting the lines below the visible number and the distillate was a completely different obstacle outside of optical character recognition and not something that I really wanted to put a year or more into figuring out.

If somebody else wants to take a crack at it, making it work with the system is just a matter of them outputting the reading at 9600 baud serial every 10 to 15 seconds. Just follow the text format as shown at the tail end of the load cell or LIDAR hydrometer code. I just don't have the spare time to put into figuring that out and how to make it simple enough for non-geek types to build.

Granted, non-geek types couldn't build the LIDAR hydrometer reader either. But, I can build it and send it to somebody so all they have to do is attach it to their parrot. The guy who designed the RPi "Hat" circuit board made things way easier to build and the LIDAR hydrometer reader simplifies things even further. If somebody else can figure out how to make an optical hydrometer reader that's also easy to build, I'd happily add it to the repository here. It's just not something that I have the time for in my schedule.

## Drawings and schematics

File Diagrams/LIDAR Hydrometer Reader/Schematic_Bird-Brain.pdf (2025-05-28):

## 38-Pin ESP32 WROOM(DA)

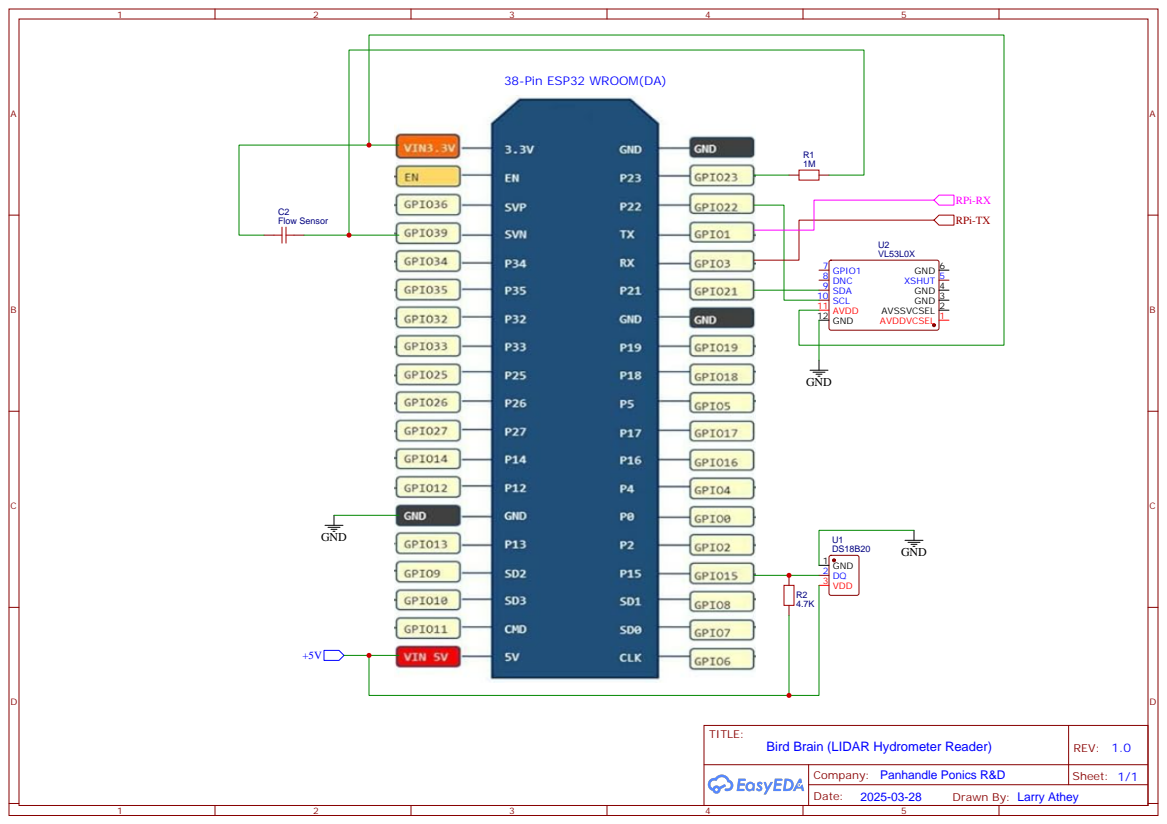
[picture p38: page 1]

Drawn By: Larry Athey

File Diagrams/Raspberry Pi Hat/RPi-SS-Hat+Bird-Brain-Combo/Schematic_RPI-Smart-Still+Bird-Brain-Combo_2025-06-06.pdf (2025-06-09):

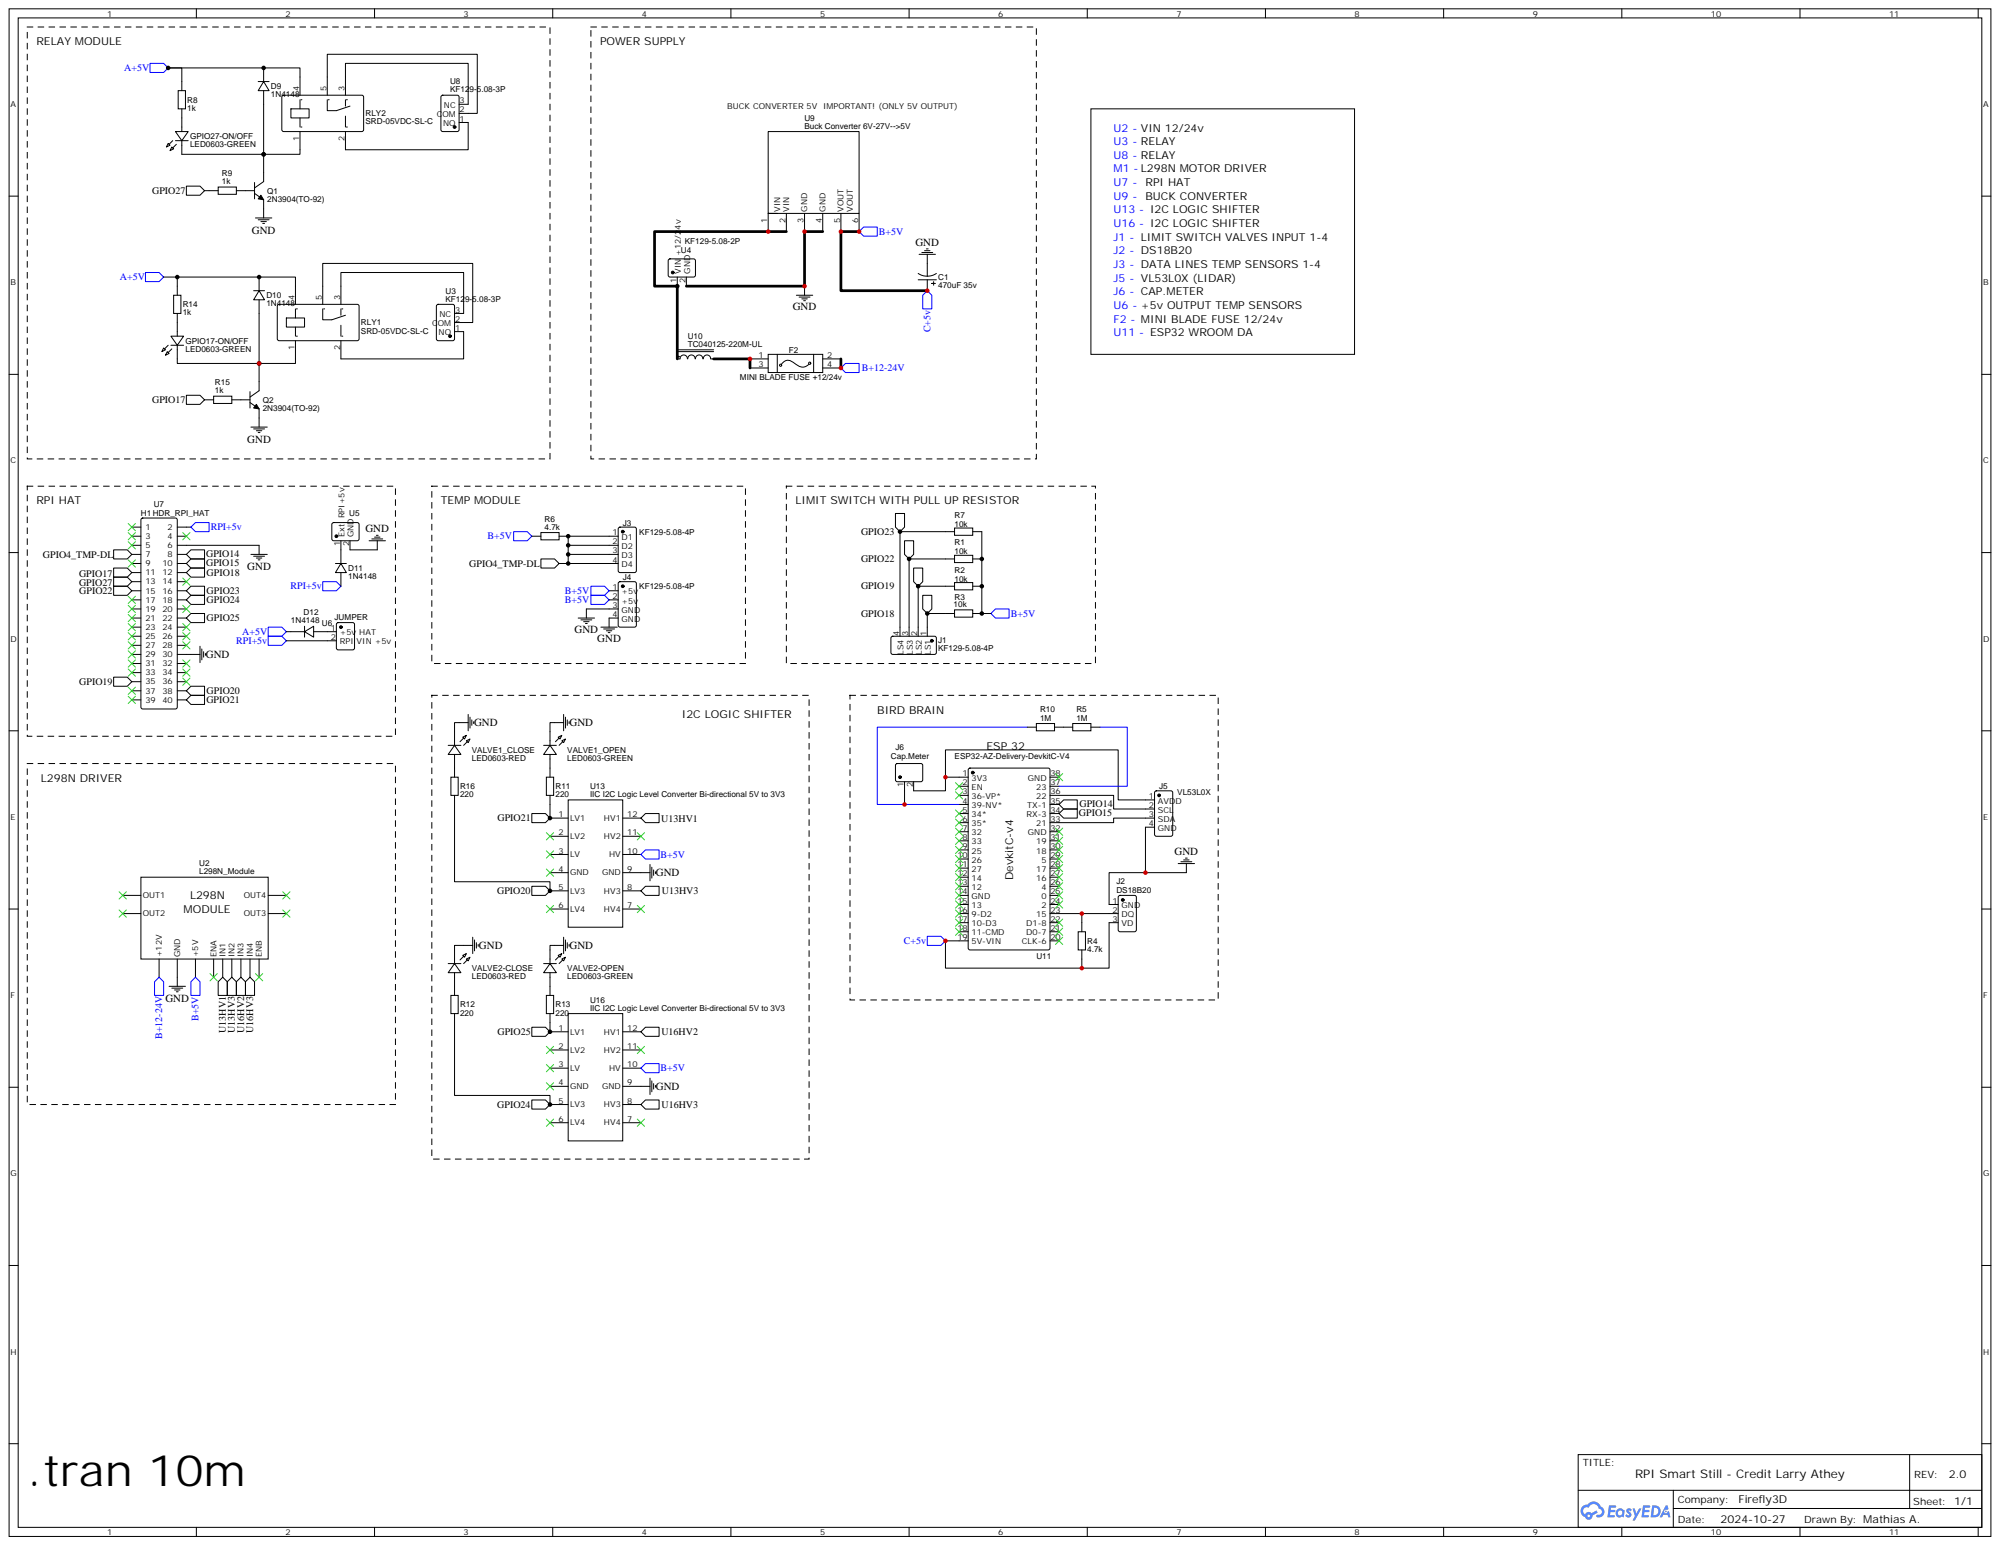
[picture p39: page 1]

BUCK CONVERTER 5V IMPORTANT! (ONLY 5V OUTPUT)

I2C LOGIC SHIFTER
LIMIT SWITCH VALVES INPUT 1-4

DATA LINES TEMP SENSORS 1-4

LIMIT SWITCH WITH PULL UP RESISTOR

IIC I2C Logic Level Converter Bi-directional 5V to 3V3

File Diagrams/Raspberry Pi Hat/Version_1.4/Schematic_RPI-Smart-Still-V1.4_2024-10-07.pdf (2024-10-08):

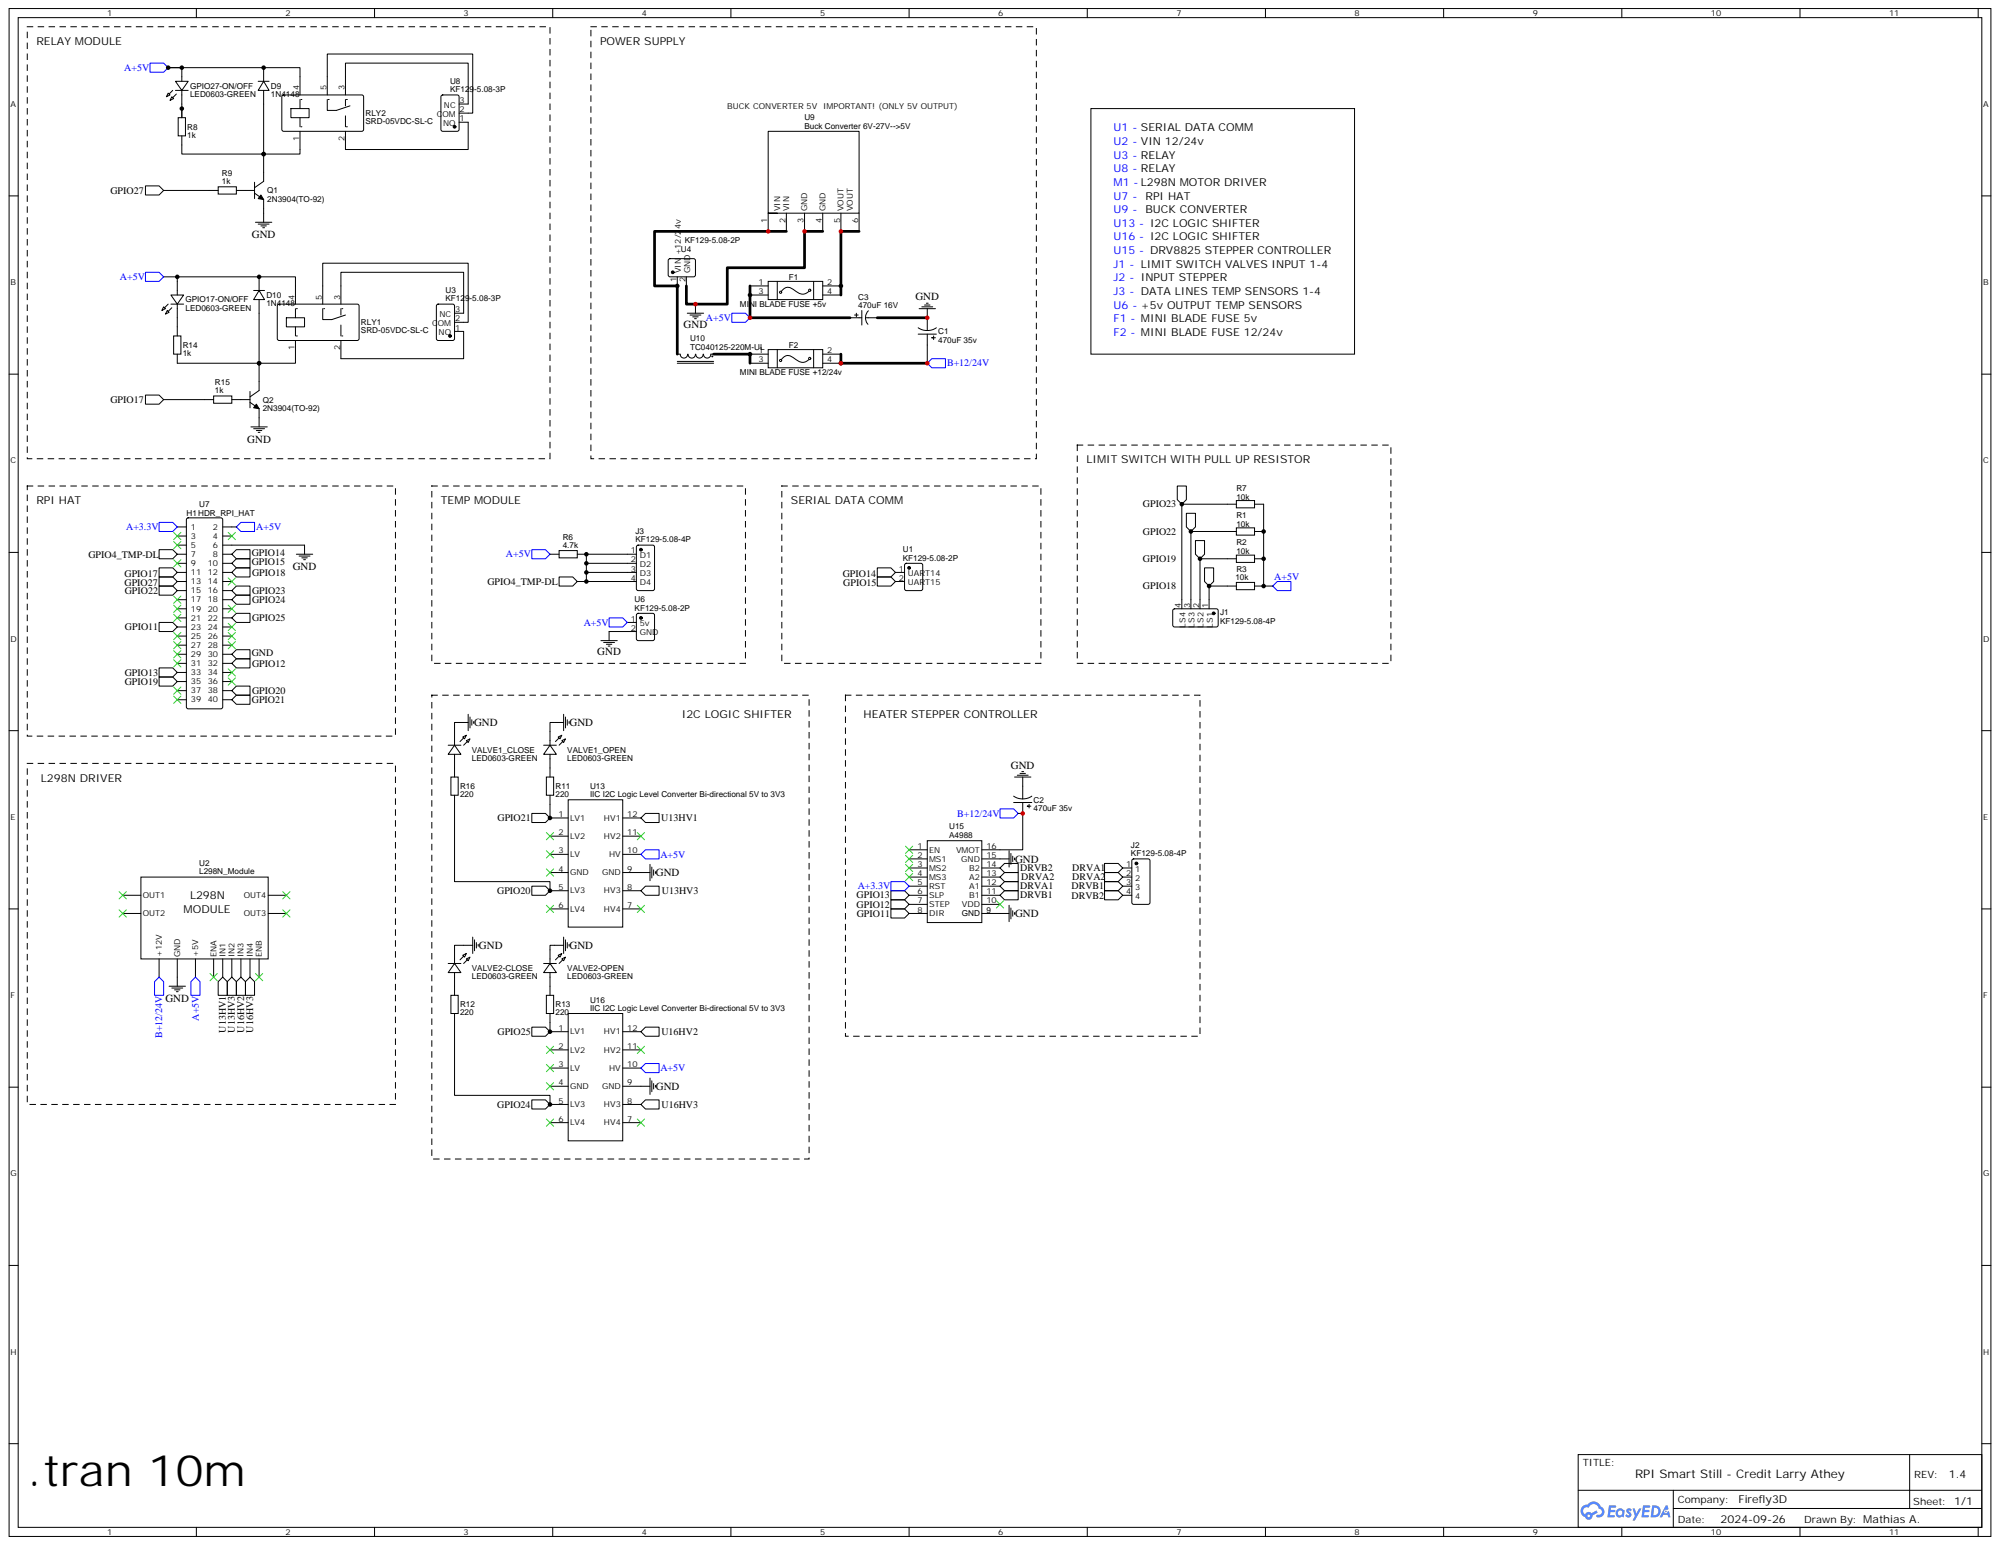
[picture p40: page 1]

BUCK CONVERTER 5V IMPORTANT! (ONLY 5V OUTPUT)

I2C LOGIC SHIFTER
DRV8825 STEPPER CONTROLLER
LIMIT SWITCH VALVES INPUT 1-4
INPUT STEPPER
DATA LINES TEMP SENSORS 1-4
+5v OUTPUT TEMP SENSORS
F1 - MINI BLADE FUSE 5v
F2 - MINI BLADE FUSE 12/24v

LIMIT SWITCH WITH PULL UP RESISTOR

IIC I2C Logic Level Converter Bi-directional 5V to 3V3

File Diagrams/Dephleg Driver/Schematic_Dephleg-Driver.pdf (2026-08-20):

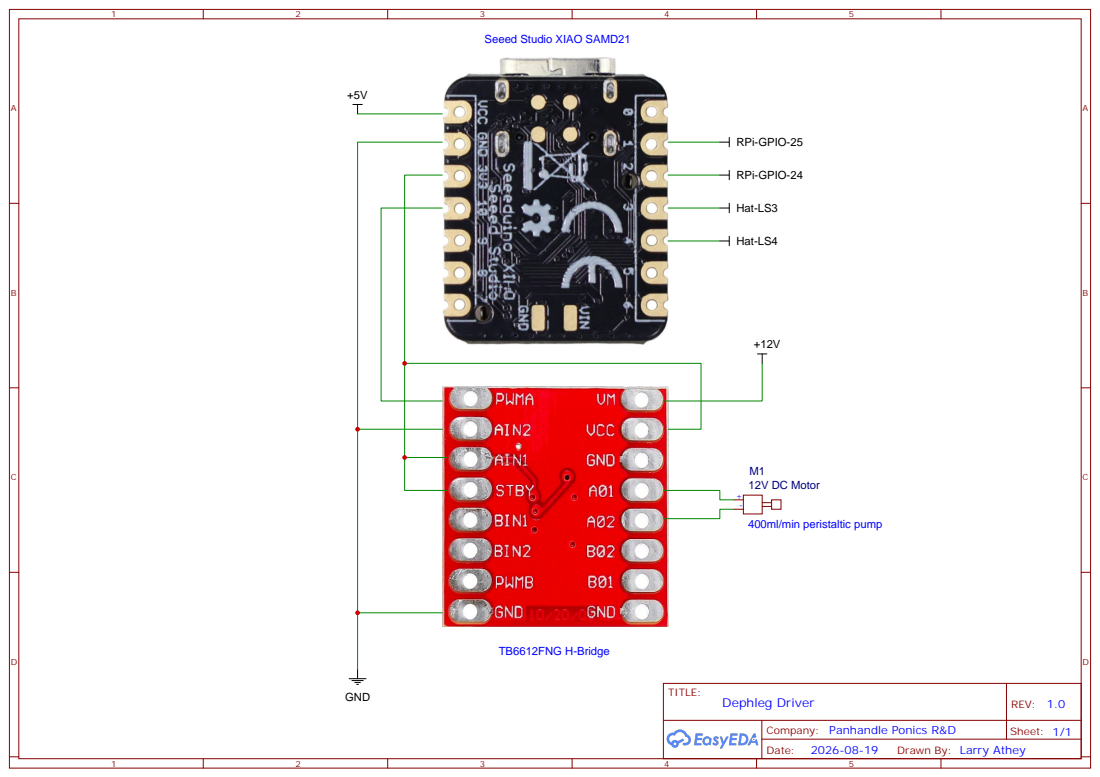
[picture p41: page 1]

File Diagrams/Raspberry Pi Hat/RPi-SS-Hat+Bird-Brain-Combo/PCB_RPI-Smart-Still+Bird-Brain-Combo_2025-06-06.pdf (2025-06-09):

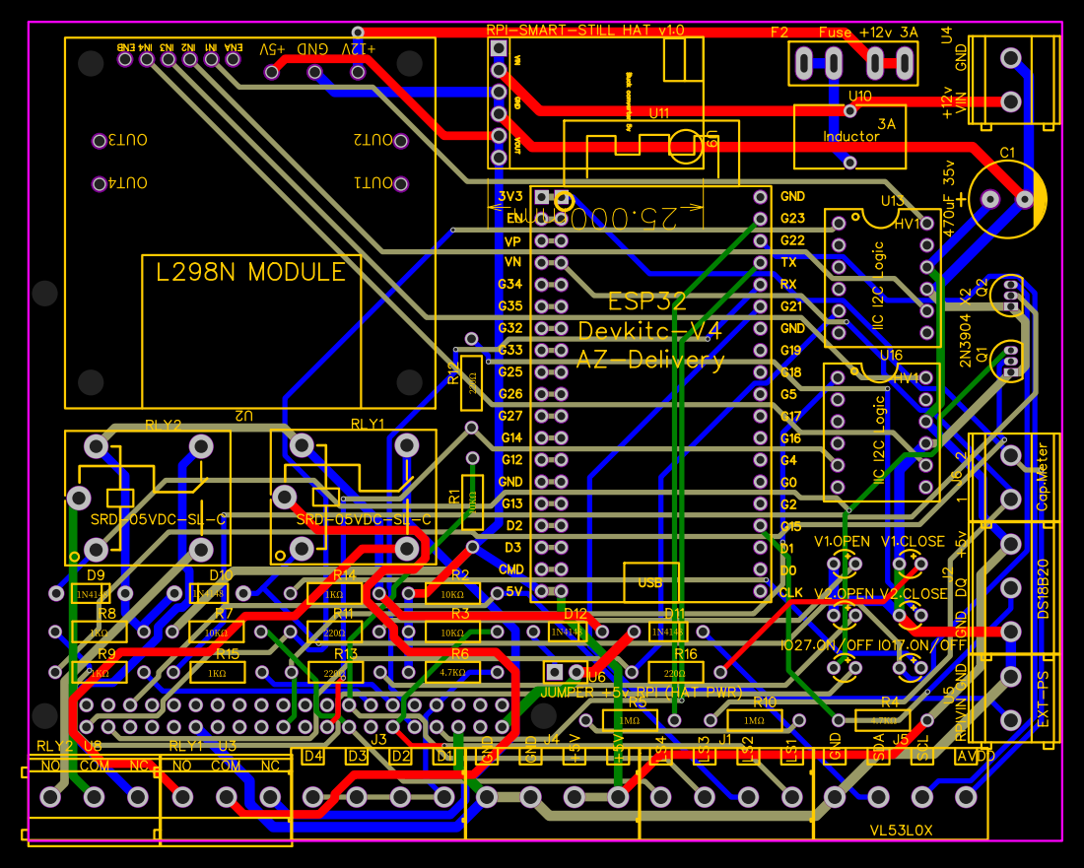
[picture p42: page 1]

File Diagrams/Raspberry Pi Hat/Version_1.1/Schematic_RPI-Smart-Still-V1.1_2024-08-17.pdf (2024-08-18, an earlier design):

### U4VIN

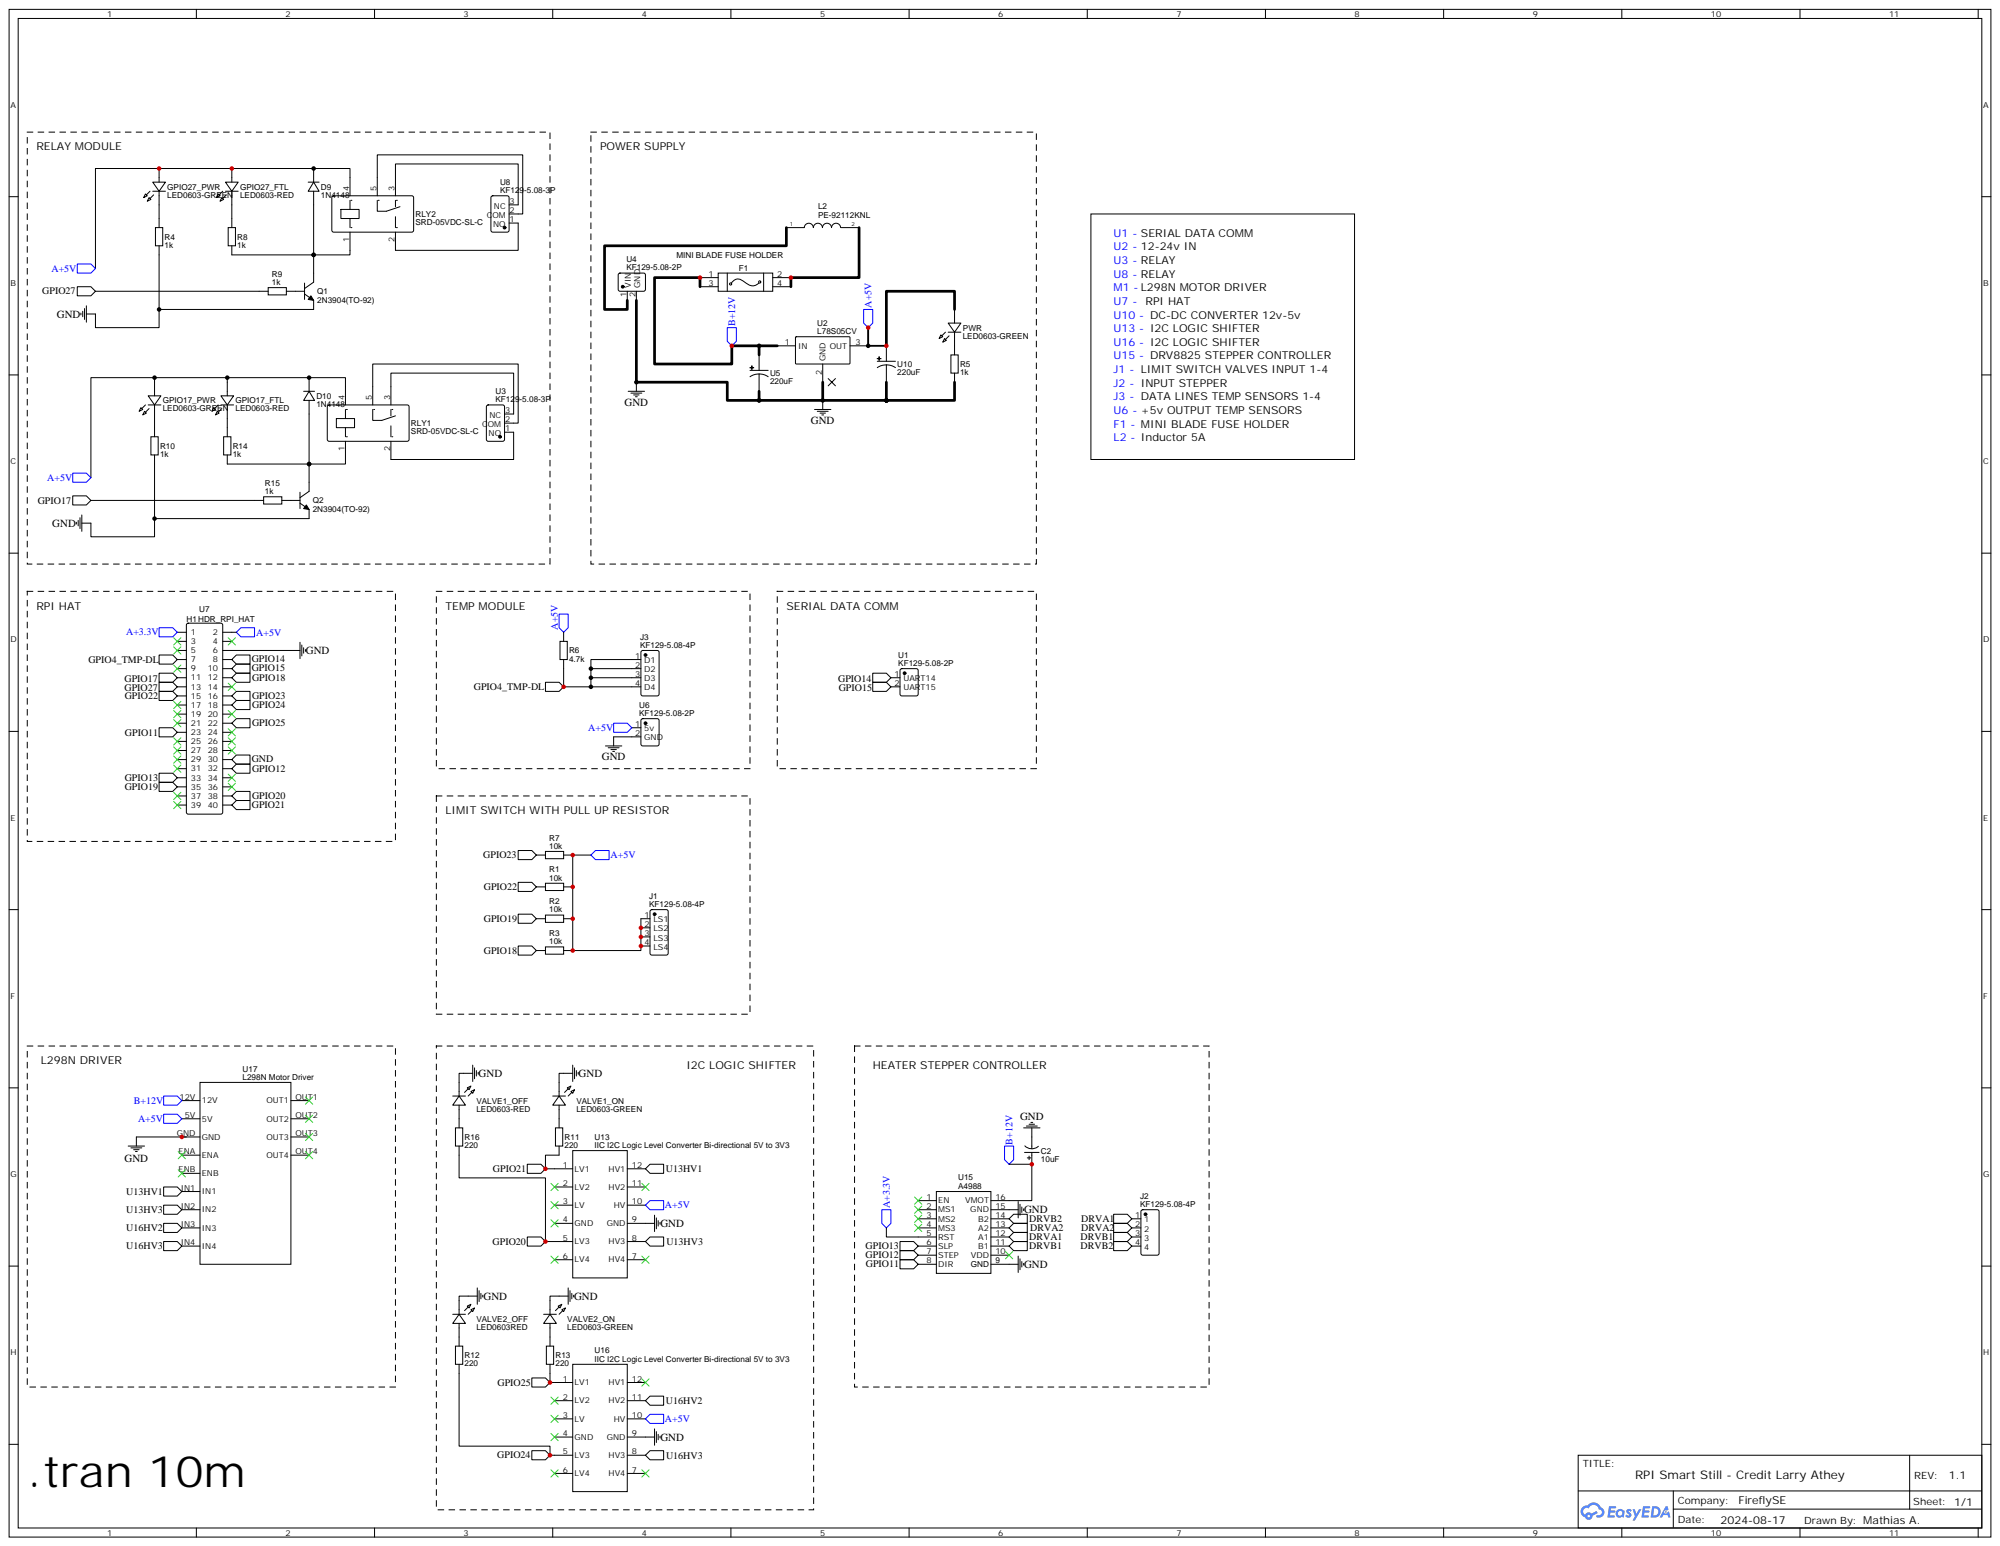
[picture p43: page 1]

SERIAL DATA COMM
RELAY
L298N MOTOR DRIVER
RPI HAT
DC-DC CONVERTER 12v-5v
I2C LOGIC SHIFTER
DRV8825 STEPPER CONTROLLER
LIMIT SWITCH VALVES INPUT 1-4
INPUT STEPPER
DATA LINES TEMP SENSORS 1-4

MINI BLADE FUSE HOLDER

+5v OUTPUT TEMP SENSORS
F1 - MINI BLADE FUSE HOLDER
L2 - Inductor 5A

LIMIT SWITCH WITH PULL UP RESISTOR

IIC I2C Logic Level Converter Bi-directional 5V to 3V3

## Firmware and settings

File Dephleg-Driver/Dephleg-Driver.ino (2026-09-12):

//------------------------------------------------------------------------------------------------
// RPi Smart Still Controller | (CopyLeft) 2024-Present | Larry Athey (https://panhandleponics.com)
//------------------------------------------------------------------------------------------------
// XIAO SAMD21 Powered Dephlegmator Cooling Valve Emulator for Peristaltic Pump
// MCU: Seeed Studio XIAO SAMD21 (Arduino IDE board name “Seeeduino XIAO”)
// Board library: https://files.seeedstudio.com/arduino/package_seeeduino_boards_index.json
//
// Emulates a US Solid motorized ball valve (10 second full travel, with limit switches)
// while driving a TB6612FNG H-Bridge feeding a 400 ml/min peristaltic pump via PWM.
//
// - Watches RPi Smart Still dephleg cooling valve OPEN / CLOSE GPIO lines
// - Accumulates actual command time so 10 ms micro-pulses are tracked
// - Advances/retracts duty by 1% for every 100 ms of command time
// - Reports limit-switch states back to the RPi Smart Still
// - Outputs PWM duty cycle 0-100% to a TB6612FNG H-Bridge
//
// This optional device may be required for those who are running a pump for their cooling water
// rather than running public utility water pressure. This is because impeller pumps don't deliver
// the necessary pressure to force water through the ball valves if they are choked down to 30% or
// lower. This prevents low volume water flow through the dephlegmator for useful reflux operation.
//
// The problem is that you can't achieve any balance between no output and switching right back to
// pot still mode. The way to solve the problem is to replace the ball valve with a peristaltic
// pump that by design has an incredibly low output volume. Rather than controlling the output of
// the pump with a valve, the speed of the motor itself is varied instead.
//
// I know what you're probably thinking...Why not just use a diaphragm pump instead? The answer is
// that while these may deliver enough pressure, they don't deliver enough volume to satisfy your
// condenser's needs. Secondly, those are not intended for continous duty and will shut down after
// a few hours due to overheating. Unlike an impeller pump, diaphragm pumps aren't water cooled.
//
// No printed circuit board is necessary since you'd still have more wires coming off this circuit
// than you would have PCB traces connecting the XIAO SAMD21 to the TB6612FNG H-Bridge. Take a look
// at the schematic in the digrams directory, it's so basic that you could glue both of the boards
// to a popsicle stick, point-to-point it in an hour, then glue it to the 3D printed pump holder.
//
// When done, there will be 7 wires (preferably 12 inches long) from the circuit to the RPi hat.
//
// Parts List:
// - Seeed Studio XIAO SAMD21: https://www.seeedstudio.com/Seeeduino-XIAO-Arduino-Microcontroller-SAMD21-Cortex-M0+-p-4426.html
// - TB6612FNG H-Bridge: https://www.amazon.com/dp/B09MJ4XPXD
// - 400ml/minute peristaltic pump: https://www.amazon.com/dp/B07HB2NM74
//
// This whole unit can be built for the same price as a half inch US Solid motorized ball valve.
// You only need to provide +12v, +5V, and GND from the RPi hat. Logic level shifter U16 (v1.3)
// is no longer needed since wires from XIAO pins 1 and 2 plug into pins 1 and 5 of the U16 socket.
// XAIO pins 3 and 4 connect to the RPi hat screw terminals LS3 and LS4. (see pin comments below)
//------------------------------------------------------------------------------------------------
const int PIN_OPEN         = 1;   // RPi-SS dephleg valve "open / forward" GPIO 25 (logic level shifter socket pin 1)
const int PIN_CLOSE        = 2;   // RPi-SS dephleg valve "close / reverse" GPIO 24 (logic level shifter socket pin 5)
const int PIN_LIMIT_OPEN   = 3;   // Simulated open limit switch (output to RPi-SS hat LS3)
const int PIN_LIMIT_CLOSED = 4;   // Simulated closed limit switch (output to RPi-SS hat LS4)
const int PIN_PWM          = 10;  // PWM output to TB6612FNG H-Bridge (PWMA or PWMB)

// Active level of the Pi control signals (true = HIGH means "move")
const bool OPEN_ACTIVE_HIGH  = true;
const bool CLOSE_ACTIVE_HIGH = true;

// Active level of the limit-switch outputs (true = LOW means "at limit")
const bool LIMIT_ACTIVE_LOW = true;

// Timing
const unsigned long MS_PER_PERCENT = 99;  // 100 ms → 1%  (10 seconds full scale), allow 1 ms for RPi GPIO latency

// Globals
int duty = 0;                     // Current position / PWM duty 0-100
unsigned long openAccum  = 0;     // Accumulated open-command time (ms)
unsigned long closeAccum = 0;     // Accumulated close-command time (ms)
unsigned long lastLoop   = 0;
//------------------------------------------------------------------------------------------------
void setup() {
  pinMode(PIN_OPEN, INPUT_PULLDOWN);
  pinMode(PIN_CLOSE, INPUT_PULLDOWN);
  pinMode(PIN_LIMIT_CLOSED, OUTPUT);
  pinMode(PIN_LIMIT_OPEN, OUTPUT);
  pinMode(PIN_PWM, OUTPUT);

  // Optional: higher PWM resolution on SAMD21 (default is usually fine)
  // analogWriteResolution(8);    // 0-255
  // analogWriteResolution(10);   // 0-1023

  lastLoop = millis();
  updateLimits();
  analogWrite(PIN_PWM, 0);

  Serial.begin(115200);
  delay(1000);
  if (Serial) Serial.println("\nXIAO Valve Emulator ready");
}
//------------------------------------------------------------------------------------------------
void updateLimits() {
  // Closed limit
  if (LIMIT_ACTIVE_LOW) {
    digitalWrite(PIN_LIMIT_CLOSED, (duty == 0) ? LOW : HIGH);
  } else {
    digitalWrite(PIN_LIMIT_CLOSED, (duty == 0) ? HIGH : LOW);
  }

  // Open limit
  if (LIMIT_ACTIVE_LOW) {
    digitalWrite(PIN_LIMIT_OPEN, (duty == 100) ? LOW : HIGH);
  } else {
    digitalWrite(PIN_LIMIT_OPEN, (duty == 100) ? HIGH : LOW);
  }
}
//------------------------------------------------------------------------------------------------
void loop() {
  unsigned long now = millis();
  unsigned long dt  = now - lastLoop;
  lastLoop = now;

  // Read Pi commands (respect active level)
  bool wantOpen  = (digitalRead(PIN_OPEN)  == HIGH) == OPEN_ACTIVE_HIGH;
  bool wantClose = (digitalRead(PIN_CLOSE) == HIGH) == CLOSE_ACTIVE_HIGH;

  // Accumulate command time only when one direction is requested
  if (wantOpen && !wantClose) {
    openAccum += dt;
    while (openAccum >= MS_PER_PERCENT && duty < 100) {
      openAccum -= MS_PER_PERCENT;
      duty++;
    }
  } else if (wantClose && !wantOpen) {
    closeAccum += dt;
    while (closeAccum >= MS_PER_PERCENT && duty > 0) {
      closeAccum -= MS_PER_PERCENT;
      duty--;
    }
  } else {
    openAccum = 0;
    closeAccum = 0;
  }
  // If both idle or both active → hold position and reset accumulators

  // Drive PWM (0-255 for 8-bit; change map() if you raised resolution)
  analogWrite(PIN_PWM, map(duty, 0, 100, 0, 255));

  // Update simulated limit switches
  updateLimits();

  if (Serial) {
    static unsigned long lastPrint = 0;
    if (now - lastPrint >= 500) {
      byte limitOpen   = digitalRead(PIN_LIMIT_OPEN);
      byte limitClosed = digitalRead(PIN_LIMIT_CLOSED);
      lastPrint = now;
      Serial.print("Duty: "); Serial.print(duty);
      Serial.print("%  OpenAcc: "); Serial.print(openAccum);
      Serial.print("  CloseAcc: "); Serial.print(closeAccum);
      Serial.print("  LimitOpen: "); Serial.print(limitOpen);
      Serial.print("  LimitClosed: "); Serial.println(limitClosed);
    }
  }
}
//------------------------------------------------------------------------------------------------

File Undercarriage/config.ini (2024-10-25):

; RPi Smart Still Configuration File
; ----------------------------------
;
; Below are the GPIO pin assignments for a Raspberry Pi 40 pin GPIO bus and the
; serial port device for the hydrometer. You may notice that Raspberry Pi clones
; also have a 40 pin GPIO bus, but their GPIO pin numbers are all out of whack.
;
; For example, Raspberry Pi Hat auxilliary relay 1, connected to physical pin 11.
;
; Raspberry Pi = GPIO 17
; Banana Pi M2 Zero = GPIO 1
;
; If you are using a Banana Pi M2 Zero, change the RELAY1=17 below to RELAY1=1.
; You will need to reboot your device after making any changes to this file.
;
; As you now know, while a clone might look like a drop-in replacement for your
; Raspberry Pi, there are times where that actually is not the case. It's best
; to test your boards by toggling pins on and off at the command line and using
; a breakout board with LEDs (link below).
;
; https://www.amazon.com/gp/product/B09QXR6RL7
;
; Refer to the link below for controlling the GPIO bus at the command line, you
; can also use this method with any Raspberry Pi clone running Linux.
;
; https://www.ics.com/blog/gpio-programming-using-sysfs-interface

; Heating stepper motor
STEPPER_ENABLE=13
STEPPER_PULSE=12
STEPPER_DIR=11
STEPPER_MS=5
; Valve 1 is the condenser valve
VALVE1_OPEN=21
VALVE1_CLOSE=20
VALVE1_LIMIT_OPEN=18
VALVE1_LIMIT_CLOSE=19
; Valve 2 is the dephlegmator valve
VALVE2_OPEN=25
VALVE2_CLOSE=24
VALVE2_LIMIT_OPEN=22
VALVE2_LIMIT_CLOSE=23
; Auxilliary relays
RELAY1=17
RELAY2=27
; Hydrometer serial port device
HYDRO_PORT=/dev/ttyAMA0
; Command to use for text-to-speech synthesis (must output to stdout)
VOICE_PROMPTER=/usr/bin/espeak -v english-us -s 160 {MSG} --stdout

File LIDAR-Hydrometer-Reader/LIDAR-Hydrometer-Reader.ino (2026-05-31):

//------------------------------------------------------------------------------------------------
// RPi Smart Still Controller | (CopyLeft) 2024-Present | Larry Athey (https://panhandleponics.com)
// Bird Brain v1.2.2 - LIDAR Hydrometer Reader and Parrot Flow Monitor - Released April 30, 2026
//
// You must be using a v2.x ESP32 library to compile this code. It appears that v3.x libraries do
// not contain compatible headers for certain legacy libraries that I rely on. You should also use
// the following URL in your preferences under Additional Boards Manager URLs.
//
// https://raw.githubusercontent.com/espressif/arduino-esp32/gh-pages/package_esp32_index.json
//
// If you have seen any of George Duncan's videos on YouTube from around 2020, you might remember
// an Arduino project of his called the "Talking Parrot Head". It involved a black PVC tube on top
// of a parrot with a VL53L0X sensor at the top that bounced the beam downward to a disc on top of
// a glass hydrometer. Depending on the distance, it would play WAV files on an SD card and speak
// the current ethanol ABV. Kind of bulky and made the parrot top heavy, but it certainly worked.
//
// While there was a window in the side near the float point, it still made the hydrometer hard to
// read visually. Yeah, I know that it was made for a blind guy. Even though I'm 50% blind, I want
// want to be able to see the hydrometer itself without the obstacle. You can just as easily shoot
// the beam upward to the bottom side of the disc on the hydrometer and turn that ABV reading into
// a digital signal that the RPi Smart Still Controller can use.
//
// The VL53L0X sensor is mounted to the side of the overflow cup of the parrot roughly even with
// the top of the overflow tube aiming upwards. A reflector equal to the diameter of the overflow
// cup is attached to the top of the hydrometer, about 20mm above the 100% line. Calibrate it with
// the RPis Smart Still Controller and you're off to the races.
//
// The reflector can be 3D printed or made out of construction paper and have hardly any effect on
// the hydrometer. Having the sensor that close to distillate isn't dangerous at all. It only runs
// on 3.3 volts and distillate isn't conductive, nor is distilled water. I've submerged one in 90%
// ethanol and distilled water while running and nothing happened, it never even stopped working.
//
// Calibration is as simple as putting the hydrometer in the parrot, add water until the 100% mark
// is even with the top of the center tube, click the button in the RPi Smart Still Controller for
// the 100% calibration. Then fill it up until the 0% mark is even with the top of the center tube
// and click the button for the 0% calibration. Calibrating the flow sensor works the same way but
// you fill it with vodka rather than water due to the dielectric properties of ethanol.
//
// The new flow sensor is a custom device designed by James (The Doc) from Ireland and determines
// the flow rate by the height of ethanol in a vessel and reading the electrical capacitance from
// two copper plates in the ethanol. The higher the flow rate, the higher the ethanol level, the
// higher the sensor reading. A perforated overflow tube controls the ethanol level in the vessel.
//------------------------------------------------------------------------------------------------
#include "Adafruit_VL53L0X.h"  // VL53L0X LIDAR sensor library by Adafruit
#include "OneWire.h"           // OneWire Network communications library
#include "DallasTemperature.h" // Dallas Temperature DS18B20 temperature sensor library
#include "Preferences.h"       // ESP32 Flash memory read/write library
//------------------------------------------------------------------------------------------------
#define ONE_WIRE 15            // 1-Wire network pin for the DS18B20 temperature sensor
#define I2C_SCL 22             // I2C clock pin
#define I2C_SDA 21             // I2C data pin
#define USER_LED 2             // Blue or Neopixel LED on the ESP32 board
//------------------------------------------------------------------------------------------------
char Uptime[10];               // Global placeholder for the formatted uptime reading
float TempC = 0;               // Global placeholder for ethanol temperature reading
float dist0 = 132.0;           // Reflector distance for 0% ABV
float dist100 = 20.0;          // Reflector distance for 100% ABV
float Distance = 0.0;          // Current LIDAR distance measurement
float emptyValue = 58.0;       // Flow sensor reading when the vessel is empty
float fullValue = 28.0;        // Flow sensor reading when the vessel is full
long SerialCounter;            // Timekeeper for serial data output updates
bool NewChip = true;           // True if the flash memory hasn't been initialized
byte EthanolBuf[10];           // Buffer for smoothing out ethanol readings
//------------------------------------------------------------------------------------------------
Adafruit_VL53L0X Lidar = Adafruit_VL53L0X();
OneWire oneWire(ONE_WIRE);
DallasTemperature DT(&oneWire);
Preferences preferences;
//------------------------------------------------------------------------------------------------
#include "flow-sensor.h"       // Inline code library for the custom capacitive flow sensor
//------------------------------------------------------------------------------------------------
void setup() {
  Serial.begin(9600);
  while (! Serial) delay(10);
  Serial.println("");

  DT.begin();
  if (! Lidar.begin(VL53L0X_I2C_ADDR,false,&Wire,Lidar.VL53L0X_SENSE_HIGH_ACCURACY)) {
    Serial.println("Failed to initialize VL53L0X");
    while(true);
  }

  // Check the flash memory to see if this is a new ESP32 and stuff it with default values if so
  GetMemory();
  if (NewChip) {
    ResetMemory();
    GetMemory();
  }

  // Set up the custom flow sensor library
  pinMode(SENSE_PIN,INPUT);
  pinMode(CHARGE_PIN,OUTPUT);
  digitalWrite(CHARGE_PIN,LOW);
  delay(100);

  pinMode(USER_LED,OUTPUT);
  SerialCounter = millis();

  for (byte x = 0; x <= 9; x ++) EthanolBuf[x] = 0;
}
//------------------------------------------------------------------------------------------------
void TempUpdate() { // Update the distillate temperature value
  DT.requestTemperatures();
  TempC = DT.getTempCByIndex(0);
}
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

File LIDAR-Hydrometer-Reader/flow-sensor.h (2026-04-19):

//------------------------------------------------------------------------------------------------
// RPi Smart Still Controller | (CopyLeft) 2024-Present | Larry Athey (https://panhandleponics.com)
// Bird Brain v1.2.2 - LIDAR Hydrometer Reader and Parrot Flow Monitor - Released April 30, 2026
// 
// This is a custom library for turning the capacitance readings from the custom flow sensor into
// a coherent 0% to 100% reading. Please use Capacitance_Meter.ino to fine tune your flow sensor.
//------------------------------------------------------------------------------------------------
#define SENSE_PIN 39  // Capacitor under test is connected between this pin and ESP32 +3.3v pin
                      // Shielded cable should be used if the capacitor connection is distant
#define CHARGE_PIN 23 // 1 or 2 meg resistor connected between this pin and SENSE_PIN
//------------------------------------------------------------------------------------------------
struct doubleLong {
  long charged_value;
  long discharged_value;
};
//------------------------------------------------------------------------------------------------
const byte chargeTime_us = 84; // ESP32 CPU instructions take ~54us
const byte dischargeTime_ms = 40;

const byte numMeasurements = 40;
const uint16_t MAX_ADC_VALUE = 4095;
const float resistor_mohm = 1.03; // 1 meg resistor seems to produce tighter capacitance values //2.035;
const float Vref = 3.3;

float capacitance_pf = 0;
float capVoltage = 0;
//------------------------------------------------------------------------------------------------
doubleLong measureADC(int num_measurements,byte charge_pin,byte sense_pin,byte charge_time_us,byte discharge_time_ms) {
  long charged_val = 0;
  long discharged_val = 0;
  for (int i = 0; i < num_measurements; i ++) {
    digitalWrite(charge_pin,HIGH); // Charge
    delayMicroseconds(charge_time_us - 54);
    charged_val += analogRead(sense_pin); // Read value and store
    digitalWrite(charge_pin,LOW); // Discharge
    delay(discharge_time_ms);
    discharged_val += analogRead(sense_pin);
    //if (analogRead(sense_pin) > 150) Serial.println("Error: discharged voltage too high");
  }
  return {charged_val /= num_measurements,discharged_val /= num_measurements};
}
//------------------------------------------------------------------------------------------------
int getFlowSensor() { // Convert the flow sensor capacitance value to a coherent flow rate
  int range = emptyValue - fullValue; // Calculate the range
  // Ensure that we're not dividing by zero
  if (range == 0) {
    return 0;
  }

  doubleLong ADCvalues = measureADC(numMeasurements,CHARGE_PIN,SENSE_PIN,chargeTime_us,dischargeTime_ms);
  capVoltage = (Vref * ADCvalues.charged_value) / (float)MAX_ADC_VALUE;
  capacitance_pf = -1.0 * ((chargeTime_us) / resistor_mohm ) / log(1 - (capVoltage / Vref));
  if (capacitance_pf > 0.0) capacitance_pf -= 9.0;

  // Calculate percentage. Since lower numbers indicate fuller, we subtract from emptyValue
  int percentage = round(((emptyValue - capacitance_pf) / range) * 100);
  // Ensure the percentage is between 0% and 100%
  return min(max(percentage,0),100);
}
//------------------------------------------------------------------------------------------------

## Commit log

2023-09-02 Create Flow Sensor Upper Housing.stl
    [Flow Sensor Upper Housing.stl]
2023-09-02 Update Flow Sensor Upper Housing.stl
    [Flow Sensor Upper Housing.stl]
2023-09-02 Create Flow Sensor Housing.stl
    [Flow Sensor Housing.stl]
2023-09-02 Create Flow Sensor Wheel.stl
    [Flow Sensor Wheel.stl]
2023-09-02 Update Flow Sensor Housing.stl
    [Flow Sensor Housing.stl]
2023-09-02 Update Flow Sensor Wheel.stl
    [Flow Sensor Wheel.stl]
2023-09-03 Create Parrot Cup Base.stl
    [Parrot Cup Base.stl]
2023-09-03 Update Parrot Cup Base.stl
    [Parrot Cup Base.stl]
2024-05-06 Create LIDAR Hydrometer Reader Cover.stl
    [LIDAR Hydrometer Reader Cover.stl]
2024-05-07 Update LIDAR Hydrometer Reader Cover.stl
    [LIDAR Hydrometer Reader Cover.stl]
2024-05-07 Create LIDAR Parrot Feed Support.stl
    [LIDAR Parrot Feed Support.stl]
2024-05-07 Create LIDAR Sensor Mount.stl
    [LIDAR Sensor Mount.stl]
2024-05-07 Update LIDAR Parrot Feed Support.stl
    [LIDAR Parrot Feed Support.stl]
2024-05-09 Create LIDAR Hydrometer Reflector Template.stl
    [LIDAR Hydrometer Reflector Template.stl]
2024-05-09 Update LIDAR Sensor Mount.stl
    [LIDAR Sensor Mount.stl]
2024-05-20 Update LIDAR Hydrometer Reflector Template.stl
    [LIDAR Hydrometer Reflector Template.stl]
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2024-09-11 Create RPi + Hat + DRV Spacers.stl
    [RPi + Hat + DRV Spacers.stl]
2024-09-11 Create RPi + Hat Mounting Plate.stl
    [RPi + Hat Mounting Plate.stl]
2024-09-12 Update RPi + Hat + DRV Spacers.stl
    [RPi + Hat + DRV Spacers.stl]
2024-09-12 Update RPi + Hat Mounting Plate.stl
    [RPi + Hat Mounting Plate.stl]
2024-09-13 Create RPi + Hat Power Breakout Mounting Plate.stl
    [RPi + Hat Power Breakout Mounting Plate.stl]
2024-09-24 Create LIDAR Hydrometer Reader Base.stl
    [LIDAR Hydrometer Reader Base.stl]
2024-09-24 Create Condenser Feed Retainer.stl
    [Condenser Feed Retainer.stl]
2024-09-24 Create Hydrometer Drilling Template.stl
    [Hydrometer Drilling Template.stl]
2024-09-24 Create Hydrometer Frame - Left.stl
    [Hydrometer Frame - Left.stl]
2024-09-24 Create Hydrometer Frame - Right.stl
    [Hydrometer Frame - Right.stl]
2024-09-24 Create Hydrometer LCD and PCB Carrier.stl
    [Hydrometer LCD and PCB Carrier.stl]
2024-09-24 Create Interface Board Mounting Plate.stl
    [Interface Board Mounting Plate.stl]
2024-09-24 Create Power Breakout Mounting Plate.stl
    [Power Breakout Mounting Plate.stl]
2024-09-24 Create Power Brick Mount.stl
    [Power Brick Mount.stl]
2024-09-24 Create Regulator Mounting Plate.stl
    [Regulator Mounting Plate.stl]
2024-09-24 Create RPI Mounting Plate.stl
    [RPI Mounting Plate.stl]
2024-09-24 Create Valve Controller Mounting Plate.stl
    [Valve Controller Mounting Plate.stl]
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2024-11-04 Create 10mm Half Tunnel Wire Guide.stl
    [10mm Half Tunnel Wire Guide.stl]
2024-11-04 Create 3-4 Flow Sensor Cap.stl
    [3-4 Flow Sensor Cap.stl]
2024-11-04 Create 3x6-2 Plastic Washers.stl
    [3x6-2 Plastic Washers.stl]
2024-11-04 Create Dual Cable Guide.stl
    [Dual Cable Guide.stl]
2024-11-04 Create Dual Hose Wall Guide.stl
    [Dual Hose Wall Guide.stl]
2024-11-04 Create Flow Sensor Plate Spacer.stl
    [Flow Sensor Plate Spacer.stl]
2024-11-04 Create Single Hose Wall Guide.stl
    [Single Hose Wall Guide.stl]
2024-11-04 Create Servo Valve Mount.stl
    [Servo Valve Mount.stl]
2024-11-08 Update 3-4 Flow Sensor Cap.stl
    [3-4 Flow Sensor Cap.stl]
2024-11-08 Update Flow Sensor Plate Spacer.stl
    [Flow Sensor Plate Spacer.stl]
2024-11-28 Create Bird Brain Flow Sensor Cap.stl
    [Bird Brain Flow Sensor Cap.stl]
2024-11-28 Create Bird Brain Overflow Sleeve.stl
    [Bird Brain Overflow Sleeve.stl]
2024-11-28 Create Bird Brain Plate Spacer.stl
    [Bird Brain Plate Spacer.stl]
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2025-01-20 Create LIDAR Sensor Mount - Back.stl
    [LIDAR Sensor Mount - Back.stl]
2025-01-20 Create LIDAR Sensor Mount - Front.stl
    [LIDAR Sensor Mount - Front.stl]
2025-01-20 Create Parrot Feed Support.stl
    [Parrot Feed Support.stl]
2025-01-20 Update LIDAR Sensor Mount - Front.stl
    [LIDAR Sensor Mount - Front.stl]
2025-01-21 Create Flow Sensor Cap.stl
    [Flow Sensor Cap.stl]
2025-01-21 Create Flow Sensor Overflow Sleeve.stl
    [Flow Sensor Overflow Sleeve.stl]
2025-01-21 Reorganizing folder names
    Reorganizing folder names
    [BOM_RPI-Smart-Still-V1.1_2024-08-17.csv, BOM_RPI-Smart-Still-V1.2_2024-09-09.csv, BOM_RPI-Smart-Still-V1.4_2024-10-07.csv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]
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2025-03-23 Create new folder for all 3/4" copper flow sensor related models
    [0.75-Pipe clamp-Half-1.stl, 0.75-Pipe clamp-Half-2.stl, 0.75-Pipe clamp-v1.3.stl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]
2025-03-23 Upload new flow sensor models
    [Flow-Sensor-Bottom.stl, Flow-Sensor-Cap.stl, Flow-Sensor-Plate-Spacer.stl]
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2025-04-08 Mounting plate update and added a new model for use with a gpio riser
    [RPi + Hat Mounting Plate (Tall).stl, RPi + Hat Mounting Plate.stl]
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2025-05-28 Bird Brain code and 3D model updates
    [Flow-Sensor-Bottom.stl, Parrot-Feed-Spacer.stl]
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2026-04-24 Replace cover frame
    [RPi-SS-Case-Frame.stl, RPi-SS-Cover-Frame.stl]
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
